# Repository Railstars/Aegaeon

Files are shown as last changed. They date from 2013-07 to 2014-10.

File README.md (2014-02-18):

Aegaeon
=======

A feature-rich, NMRA standards compliant DCC decoder built around the Atmel ATtiny84A.

This project comprises hardware, firmware, and documentation for the Railstars Aegaeon series of [NMRA DCC decoders](http://en.wikipedia.org/wiki/Digital_Command_Control).

The Intent
----------

Let's be honest: Most decoders manufactured in North America kinda suck. We can do better. I want to harness the power of open source development to put together the finest range of decoders available, anywhere. This project has multiple goals:
* NMRA standard conformance
* Robustness: decoders should be fault-tolerant, and compatible with widest range of other DCC equipment
* Size: Modern technology permits really tiny decoders
* Features: There is no excuse not to have the best feature set possible

Hardware
--------

The hardware features an Atmel ATtiny84A microcontroller, a high-current H-Bridge with BEMF feedback, and two high-current open-collector outputs for lighting effects.

### Features

* Ultra-compact size (approx. 11mm x 6.7mm)
* 1A motor outputs
* Feedback motor control (aka BEMF)
* 16KHz or 32KHz motor operating modes
* Two high-current (300mA) function outputs
* Debugging header for use with DEBUGwire devices like Atmel JTAGICE mk2
* Trimming of internal RC oscillator is necessary for operation, requires Atmel AVRISP, a copy of stk500.exe, and MS DOS to calibrate. (Welcome to the 21st century!)

Firmware
--------

The firmware is written in pure C, and can be conditionally compiled for one of three possible configurations (motor only; motor + two functions; H-Bridge-driven function-only). Feature packed, and fully NMRA standards compliant, guaranteed by a stringent set of unit tests (in UnitTests folder, includes Xcode and NetBeans projects so you can run them straight on your Mac or PC).

### Features

* Momentum, 3-step and 28-step speed tables
* Button-controllable shunting mode
* Configurable function directionality, brightness, and Rule 17 dimming effects
* Configurable, button-controllable animations:
    * Strobe
    * Double strobe
    * Rotary beacon
    * Random flicker
    * Left/right ditch lights
    * Mars and Gyra lights
* Optional soft-start lighting effect
* Advanced consisting
* Supports Paged, Direct, Physical, and Operations mode programming
* Configurable DC operation, or stop-on-DC.

License
-------

The contents of the firmware folder is licensed under the GPLv3.
All other content is licensed under a Creative Commons Attribution-ShareAlike 3.0 Unported license

The Future
----------

There are a large number of features I would like to add to this product. I need your help!
- [ ] 2-layer PCB with easy-to-solder components for DIY
- [ ] ATmega328p/AT90CAN128 support for Arduino Uno/Railstars Io:duino
- [ ] Visual Studio project for unit tests
- [ ] Arduino project for easy integration into Arduino projects
- [ ] RailCom support (Railstars has a license to the necessary patents to implement RailCom, need to verify that implementing it as an open source project is kosher)
- [ ] On-the-tracks ops-mode bootloader. Ideally Arduino compatible but that might be a stretch. Would certainly require RailCom to work. But wouldn't that be awesome!?

Discussion
----------

You can get support for the Aegaeon software at the Railstars [Support Forum](http://support.railstars.com/index.php?p=/categories/aegaeon-firmware)

Bitdeli Badge (https://bitdeli.com/free "Bitdeli Badge")

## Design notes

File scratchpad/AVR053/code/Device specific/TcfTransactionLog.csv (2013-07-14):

Service | Message | Max | Min | Average | Count | frequency | TimedOut
Stream | setLogBits | 218.3916 | 218.3916 | 218.3916 | 1 | 0

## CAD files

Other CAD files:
scratchpad/AVR053/code/rc_calib.obj

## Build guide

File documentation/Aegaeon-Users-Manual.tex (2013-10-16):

%! program = pdflatex

\documentclass[12pt,letterpaper,draft]{memoir} % for a short document

\usepackage{longtable}
\usepackage{multirow}
\usepackage{url}
\usepackage{makeidx}
\usepackage{etoolbox}

% See the ``Memoir customise'' template for some common customisations
% Don't forget to read the Memoir manual: memman.pdf

\makepagestyle{manual}
\makeevenhead{manual}{}{}{\rightmark}
\makeoddhead{manual}{\rightmark}{}{}
\makeheadrule{manual}{\textwidth}{0.4pt}
\makeevenfoot{manual}{\thepage}{}{\leftmark}
\makeoddfoot{manual}{\leftmark}{}{\thepage}
\makefootrule{manual}{\textwidth}{0.4pt}{\footruleskip}

\makeoddfoot{plain}{}{}{\thepage}
\makeevenfoot{plain}{\thepage}{}{}
\makefootrule{plain}{\textwidth}{0.4pt}{\footruleskip}

\makeatletter
\aliaspagestyle{title}{empty} % suppress the page number after \maketitle
\let\origps@chapter\ps@chapter
\preto\frontmatter{\let\ps@chapter\ps@empty\pagestyle{empty}}
\preto\mainmatter{%
  \cleardoublepage
  \let\ps@chapter\origps@chapter\pagestyle{headings}}
\makeatother

\title{Aegaeon Family User's Manual\\Revision A}
\author{Railstars Limited}
%\date{} % Delete this line to display the current date

\makeindex

%%% BEGIN DOCUMENT
\begin{document}
\maketitle
\newpage

\chapter*{Acknowledgments}

Many people have made Aegaeon possible, and deserve recognition. First of all, Railstars sends its deepest gratitude to the fine folks at \url{http://jnsforum.com}, where this project was conceived, for all their support and encouragement. Thanks especially to Stuart Baker for his feedback and advice during the design stages. A huge thanks to our testers, Timothy Hatch and Ken Shores, without whose help many bugs would have remained unconvered. Ken's assistance in editing this document was also invaluable. And a thanks to my regular employers, Screenhero, Inc., for their encouragement in completeing this project.

Most of all, however, deepest thanks go to Amy Goodman-Wilson and Acadia Goodman-Wilson, whose love and support throughout this process (as well as their tolerance for flux fumes!) will be forever remembered.
\newpage

\tableofcontents* % the asterisk means that the contents itself isn't put into the ToC

\pagestyle{manual}
%%%%%%%%%%%%%%%%%%%%%%%%%%%%%%%%%%%%%%%%%%%%%%%%%%%%%%%%%%%%%%%%%%%%%%%%%%%%%%%%%%%%
%%%%%%%%%%%%%%%%%%%%%%%%%%%%%%%%%%%%%%%%%%%%%%%%%%%%%%%%%%%%%%%%%%%%%%%%%%%%%%%%%%%%
%%%%%%%%%%%%%%%%%%%%%%%%%%%%%%%%%%%%%%%%%%%%%%%%%%%%%%%%%%%%%%%%%%%%%%%%%%%%%%%%%%%%
\chapter{Introduction}

Thank you for purchasing a Railstars Aegaeon digital decoder! With a little care and feeding, your decoder should offer a lifetime of service. We are certain you will be well-pleased.

The Railstars Aegaeon family of digital decoders are the most advanced ultra-compact decoders on the market today. Despite their diminutive size, the Aegaeon family provides unprecedented fine-grain control over every aspect of their operation and configuration, as well as the same high level of robustness you expect from Railstars.

This manual covers everything you need to know about the Aegaeon:L2, Aegaeon:M, and Aegaeon:C digital decoders. Chapter \ref{installation} covers installation of your decoder. Chapters \ref{generalconfiguration}, \ref{motorconfiguration}, and \ref{specialeffectsconfiguration} cover the wide range of configuration options available on your decoder. Chapter \ref{operations} covers operating your decoder on your layout. Finally, Chapter \ref{troubleshooting} covers the steps you should take when something goes wrong.

\section{What's In a Name?}

The Aegaeon family of digital decoders is named for one of Saturn's moons. This natural satellite is Saturn's smallest moon, and is considered the source of one of Saturn's rings. The moon was, in turn, named for one of the hundred-armed giants of Greek mythology, the hecatonchires, who helped overthrow the Titans. Seems a fitting name to us!

%%%%%%%%%%%%%%%%%%%%%%%%%%%%%%%%%%%%%%%%%%%%%%%%%%%%%%%%%%%%%%%%%%%%%%%%%%%%%%%%%%%%
%%%%%%%%%%%%%%%%%%%%%%%%%%%%%%%%%%%%%%%%%%%%%%%%%%%%%%%%%%%%%%%%%%%%%%%%%%%%%%%%%%%%
%%%%%%%%%%%%%%%%%%%%%%%%%%%%%%%%%%%%%%%%%%%%%%%%%%%%%%%%%%%%%%%%%%%%%%%%%%%%%%%%%%%%
\chapter{Tools \& Installation}
\label{installation}
Each of the various decoders in the Aegaeon family serves a specific purpose, and therefore each is installed in a slightly different manner. The following sections will help you to choose the best decoder for your project, and guide you through the installation proceedure.

%%%%%%%%%%%%%%%%%%%%%%%%%%%%%%%%%%%%%%%%%%%%%%%%%%%%%%%%%%%%%%%%%%%%%%%%%%%%%%%%%%%%
\section{Choosing the Right Decoder}

Each member of the Aegaeon family is designed for a specific purpose. Choose the right decoder for the right task.

\begin{description}
\item[Aegaeon:L2] is designed to drive a single motor and up to two LEDs or bulbs.
\item[Aegaeon:M] is designed to drive a single motor, without any lighting.
\item[Aegaeon:C] is designed for lit cab cars, passenger cars with marker lights, or lit dummy locomotives---anything without a motor. The :C is especially designed for models whose lighting circuits are too small or complicated to cut up (most other DCC decoders require you to partially dismantle the lighting circuits).
\end{description}

Each of these decoders is best suited to a particular kind of model:
\begin{description}
\item[Locomotive with headlights] Aegaeon:L2
\item[Locomotive without headlights] Aegaeon:M
\item[``Helper'' motorized boxcar] Aegaeon:M
\item[Self-propelled passenger unit] Aegaeon:M (if unlit) or Aegaeon:L2 (if lit)
\item[Business car with marker lights] Aegaeon:C
\item[Observation passenger car with marker lights] Aegaeon:C
\item[Unpowered cab unit] Aegaeon:C
\item[Dummy locomotive with lights] Aegaeon:C
\end{description}

%%%%%%%%%%%%%%%%%%%%%%%%%%%%%%%%%%%%%%%%%%%%%%%%%%%%%%%%%%%%%%%%%%%%%%%%%%%%%%%%%%%%
\section{Tools}

If you have never installed a wire-in decoder before, you will find that a good set of tools and a familiarization with the procedure will make the job immeasurably easier. If you have never soldered before, you might find purchasing a beginner's electronics kit (such as those available from Velleman or Sparkfun) excellent practice without risking your expensive models first.

\begin{description}
\item[Soldering iron] with a reasonably fine tip and a good, wet sponge for cleaning the tip. An inexpensive 30W iron from Radio Shack is a fine starting point.
\item[Solder] containing either 60/40 or (preferably) 63/37 tin/lead ratio, with a rosin core. 0.8mm (0.032in) diameter is about right.
\item[Wire strippers] capable of stripping 30AWG wire.
\item[Safety goggles] because hot solder in the eyes stings pretty bad.
\item[Anti-static or grounding strap] to prevent static shocks from destroying your investment.
\item[Needle-nosed pliers] for when your fingers are too big and soft to hold on tight.
\item[Third hand]---not a real one, although that can be helpful too, but the kind that features several alligator clips on a positionable rail. Look to the local fly-fishing outfitter for an inexpensive model.
\item[Heat-proof work surface] such as an old cutting board. Please do not use this cutting board for food after it has been used for electronics work! Lead poisoning is serious stuff.
\item[Kapton tape] or polyamide tape is useful for electrically isolating large surfaces.
\item[Soldering heat sinks] which look like small, flat-surfaced alligator clips, and are useful for when you have to solder to a surface that makes contact with something meltable nearby.
\item[Continuity checker of multimeter] for checking your solder connections and testing for short circuits.
\item[Jeweler's screw-drivers] in both Phillips (cross) and flat heads.
\item[Spudger] for prying at plastic shells and smoothing wires. This is a pencil-like tool made from nylon, usually with a pointed end and a flatted end. Optional, but helpful.
\item[Jeweler's files] in case you need to make small modifications to the metal frame.
\item[Dremel] or similar, with bits for grinding soft metal. Such a tool is for milling out a larger space in any internal metal frame, which is often necessary in many small-scale locomotives.
\end{description}

%%%%%%%%%%%%%%%%%%%%%%%%%%%%%%%%%%%%%%%%%%%%%%%%%%%%%%%%%%%%%%%%%%%%%%%%%%%%%%%%%%%%
\section{Preparing the Model}

If you have never had your model apart before, this is a good time to familiarize yourself with how the model comes apart and fits together. One common mistake is to reach a point where an installation is nearly complete, only to find that the plastic shell no longer fits back on the model!

While the model is apart, assess it for potential locations to site the decoder. Consider not just the open spaces inside the model, but areas in the frame that could be milled away to create space for the decoder too. Be sure to give an eye to where and how the various wires will run, and whether you will need to cut channels for them in any of the parts to ensure good fit.

While the model is apart, check to see if the manufacturer has placed a capacitor across the motor brushes. Most capacitors appear as a flat tan disk. Although such are rare, if you do see one, it should be removed.

Once the decisions have been made, and you are certain how the model goes together, we can begin with the installation itself.

%%%%%%%%%%%%%%%%%%%%%%%%%%%%%%%%%%%%%%%%%%%%%%%%%%%%%%%%%%%%%%%%%%%%%%%%%%%%%%%%%%%%
\section{Installing Aegaeon:L2}

% TODO write this

The Aegaeon:L2 is designed for TODO and is the most difficult decoder to install. Installation consists of the following steps:
\begin{enumerate}
\item Make space for the decoder.
\item Make space for the wires and trim to length.
\item Isolate the motor from the frame.
\item Isolate the lighting board(s).
\item Solder decoder to the frame or brass/copper pickups.
\item Solder decoder to the motor.
\item Solder decoder to the lighting board(s).
\item Route wires.
\item Test.
\item Reassemble model.
\end{enumerate}

% TODO need to say something about checking stall current, use of resistors with LEDs, lots of diagrams, etc. Also use of bulbs and potential for overheating on DCC.

%%%%%%%%%%%%%%%%%%%%%%%%%%%%%%%%%%%%%%%%%%%%%%%%%%%%%%%%%%%%%%%%%%%%%%%%%%%%%%%%%%%%
\section{Installing Aegaeon:M}

The Aegaeon:M is designed to be a reasonably easy decoder to install. Installation consists of the following steps:
\begin{enumerate}
\item Measure stall current.
\item Make space for the decoder.
\item Make space for the wires and trim to length.
\item Isolate the motor from the frame.
\item Solder decoder to the frame or brass/copper pickups.
\item Solder decoder to the motor.
\item Route wires.
\item Test.
\item Reassemble model.
\end{enumerate}

\subsection{Measure Stall Current}
Aegaeon:M is designed to provide as much as 800mA of current continuously, although most N and HO motors draw far less than that under normal operating conditions. The worst-case draw of a motor is its ``stall current'', that is, the current that it draws when full power is applied, but the motor shaft is held firmly still (which, please note, does not constitute ``normal operating conditions''!). Most modern models will have a stall current well below 800mA, but it is easy to check if you have a multimeter or ammeter.

With the ammeter or multimeter wired in series between the power pack and the track, apply full DC voltage while holding the locomotive firmly down on the tracks. The goal is to prevent the wheels from spinning or slipping, thus stalling the motor. Observe the meter's reading. If it is greater than 800mA, consider using a more powerful decoder than the Aegaeon:M.

\subsection{Make Space for the Decoder}
Many larger models will have plenty of open space inside of them where the decoder could be sited. However in N and Z scales, the options are (both literally and figuratively) much narrower. In many cases, you will have to create a pocket for the decoder by milling out a portion of the metal frame. If you have a hard time determining where to site your Aegaeon:M, consider visiting the Railstars Support Site at \url{http://support.railstars.com}. This website offers a range of pictorial instructions for installing Aegaeon decoders, as well as a friendly support forum where you can ask other Aegaeon users for advice.

\subsection{Make Space for the Wires and Trim to Length}
Siting the decoder is only half the battle. The Aegaeon:M has four wires that must also be positioned. It is quite likely that you may have to cut channels in the metal frame or internal plastic supports to make room for the wires---they may look small, but space is tight inside your model!

First, identifying where each of the four wires can be most easily connected to the model. The Red and Black wires collect the DCC signal and power from the tracks, and will need to be wired to the internal current collectors (some times called pick-ups)---the bits of metal that make electrical contact with the rails. The Orange and Gray wires control the motor, and will need to be wired to the motor brushes. See Figure \ref{M-wiring} for an example of how to wire the Aegaeon:M.

%TODO figure \label{M-wiring}

Holding the Aegaeon:M in place with a little double-sided tape, develop a careful plan for routing each lead. Once you have a satisfactory notion of where each will go, trim back any excess length. Otherwise, all that extra wire is going to need space of its own.

\subsection{Isolate the Motor from the Frame}
Normally, the motor's brushes make electrical contact with the two rails (usually indirectly via the frame, or other metal conductors within the model). Installing the Aegaeon:M requires that we break this connection, so that the decoder can control the motor directly. Find the points of electrical contact between the motor brushes and the rest of the model (often inside the metal frame, but sometimes with soldered wires or other mechanisms). Trim back any wires or long leads connecting the motor to the rest of the model, and use Kapton tape as insulation where the electrical contact is achieved via press-fit (a single layer of tape will suffice).

Sometimes it is not obvious how to isolate the motor. If you find yourself stumped, don't forget about the Raisltars Support Site at \url{http://support.railstars.com}, where you can view pictorial installation guides and ask for advice from other Aegaeon users.

Make sure that the motor really is isolated, using a continuity tester where possible. On some models, it may be nearly impossible to test that the motor is isolated. One simple, but not perfectly reliable, method is to reassemble the model, and see if you can make it move with a standard DC throttle. If the motor does not respond to the throttle, there is a good chance is has been successully isolated; if the motor \textit{does} respond, you have not yet achieved the necessary isolation.

\subsection{Solder Red and Black Wires to the Pickups}
Once the motor is isolated, begin connecting the decoder by soldering in the Red and Black wires. You should have, in an earlier step, identified the best place to connect these wires. Now, the time has come to solder these wires to the internal current collectors that make electrical contact with the rails.

\subsection{Solder Orange and Gray Wires to the Motor Brushes}

The Orange and Gray wires control the motor. Now that we are certain that the motor is isolated from the rails, and the decoder is connected to the rails, solder the Orange and Gray wires to the motor leads.

Once connected, this is a good time to make your first real test. You do not need to fully reassemble the model for this step; but you will need to be able to place it on a programming track. Once on the programming track, attempt to read one of the CVs (see \S\ref{WhatIsACV} for details on what a CV is, and how to read them). If you can read the selected CV, the test is passed. If you cannot, then either the decoder is not making good electrical contact with the rails, or with the motor. In this case, use a continuity checker to determine where the break in the circuit might be.

Once you can read CVs, try placing your model on the main line and controlling it with your DCC throttle. The model should respond to speed commands normally. If not, this is a good sign that your connections are perhaps loose, or you have a cold solder joint that needs to be reworked.

\subsection{Route Wires and Affix Decoder}

Once you are certain that the decoder is wired in securely and properly, route the wires into the channels (if you needed to make channels). A spudger comes in handy for telling wires just where they need to go, and pressing them flat into the channels. Use a little double-sided tape to secure the decoder in place, making sure that it is not touching any metal surface; use some Kapton tape if necessary to provide some electrical isolation. You can tape the metal surfaces in the mode near the decoder site, or wrap the decoder in the tape.

\subsection {Test. Test. Test.}

Once everything is in place, repeat all of the tests above. Try reading and writing CVs; give the model a spin on the main line. Everything should run as expected. If not, don't be discouraged! Better to find out that something has gone wrong now, than after the model has been put back together! Again, if something isn't working, a continuity checker is going to be your best tool for isolating problems.

\subsection{Final Reassembly and Test Again}

Even once the model has passed all the tests with flying colors, your work is not yet done. Reassembling the model is not always easy. It might reveal that you didn't leave enough room for the decoder, or the wires. It might also reveal that one of the connections is still a bit loose, and comes apart under pressure from the plastic shell. Both problems are often easy to spot, because the plastic shell will bulge from the pressure of the installed decoder.

%%%%%%%%%%%%%%%%%%%%%%%%%%%%%%%%%%%%%%%%%%%%%%%%%%%%%%%%%%%%%%%%%%%%%%%%%%%%%%%%%%%%
\section{Installing Aegaeon:C}

The Aegaeon:C is designed to control simple DC lighting boards, and hence is probably the easiest decoder to install. Installation consists of the following steps:
\begin{enumerate}
\item Make space for the decoder.
\item Make space for the wires and trim to length.
\item Isolate the lighting board from the frame.
\item Solder decoder to the frame or brass/copper pickups.
\item Solder decoder to the lighting board.
\item Route wires.
\item Test.
\item Reassemble model.
\end{enumerate}

\subsection{Make Space for the Decoder}
Many larger models will have plenty of open space inside of them where the decoder could be sited. However in N and Z scales, the options are (both literally and figuratively) much narrower. In many cases, you will have to create a pocket for the decoder by milling out a portion of the metal frame. If you have a hard time determining where to site your Aegaeon:M, consider visiting the Railstars Support Site at \url{http://support.railstars.com}. This website offers a range of pictorial instructions for installing Aegaeon decoders, as well as a friendly support forum where you can ask other Aegaeon users for advice.

\subsection{Make Space for the Wires and Trim to Length}
Siting the decoder is only half the battle. The Aegaeon:C has four wires that must also be positioned. It is quite likely that you may have to cut channels in the metal frame or internal plastic supports to make room for the wires---they may look small, but space is tight inside your model!

First, identifying where each of the four wires can be most easily connected to the model. The Red and Black wires collect the DCC signal and power from the tracks, and will need to be wired to the internal current collectors (some times called pick-ups)---the bits of metal that make electrical contact with the rails. The White and Yellow wires control the lighting, and will need to be wired to the two leads on the lighting circuit board. See Figure \ref{C-wiring} for an example of how to wire the Aegaeon:C.

%TODO figure \label{C-wiring}

Holding the Aegaeon:M in place with a little double-sided tape, develop a careful plan for routing each lead. Once you have a satisfactory notion of where each will go, trim back any excess length. Otherwise, all that extra wire is going to need space of its own.

\subsection{Isolate the Lighting Board from the Frame}
Normally, the lighting board's leads make electrical contact with the two rails (usually indirectly via the frame, or other metal conductors within the model). Installing the Aegaeon:C requires that we break this connection, so that the decoder can control the lighting board directly. Find the points of electrical contact between the lighting board leads and the rest of the model (often via simple contact with the metal frame, but sometimes with soldered wires or other mechanisms). Trim back any wires or long leads connecting the lighting board to the rest of the model, and use Kapton tape as insulation where the electrical contact is achieved via press-fit (a single layer of tape will suffice).

Sometimes it is not obvious how to isolate the lighting board. If you find yourself stumped, don't forget about the Raisltars Support Site at \url{http://support.railstars.com}, where you can view pictorial installation guides and ask for advice from other Aegaeon users.

Make sure that the lighting board really is isolated, using a continuity tester where possible. On some models, it may be nearly impossible to test that the lighting board is isolated. One simple, but not perfectly reliable, method is to reassemble the model, and see if you can make it light up with a standard DC throttle. If the lighting does not respond to the throttle, there is a good chance is has been successully isolated; if the lighting \textit{does} respond, you have not yet achieved the necessary isolation.

\subsection{Solder Red and Black Wires to the Pickups}
Once the motor is isolated, begin connecting the decoder by soldering in the Red and Black wires. You should have, in an earlier step, identified the best place to connect these wires. Now, the time has come to solder these wires to the internal current collectors that make electrical contact with the rails.

\subsection{Solder White and Yellow Wires to the Lighting Board Leads}

The White and Yellow wires control the lighting board. Now that we are certain that the lighting board is isolated from the rails, and the decoder is connected to the rails, solder the White and Yellow wires to the lighting board leads.

Once connected, this is a good time to make your first real test. You do not need to fully reassemble the model for this step; but you will need to be able to place it on a DCC-controlled main line. Once on the main line, attempt to control the model with your DCC throttle set to DCC address 3. The lighting should come on, and respond to throttle direction changes. If you can so control the lighting, the test is passed. If you cannot, then either the decoder is not making good electrical contact with the rails, or with the lighting board. In this case, use a continuity checker to determine where the break in the circuit might be.

Unfortunately, the usual programming-track test won't always work with the Aegaegon:C, because reading a CV requires a certain amount of current draw from the programmer. Many modern models use highly efficient LED lighting, which does not draw sufficient current to provide the feedback that the DCC programmer is expecting. Thus, we can only test reliably on the main line.

\subsection{Route Wires and Affix Decoder}

Once you are certain that the decoder is wired in securely and properly, route the wires into the channels (if you needed to make channels). A spudger comes in handy for telling wires just where they need to go, and pressing them flat into the channels. Use a little double-sided tape to secure the decoder in place, making sure that it is not touching any metal surface; use some Kapton tape if necessary to provide some electrical isolation. You can tape the metal surfaces in the mode near the decoder site, or wrap the decoder in the tape.

\subsection {Test. Test. Test.}

Once everything is in place, repeat all of the tests above. Try reading and writing CVs; give the model a spin on the main line. Everything should run as expected. If not, don't be discouraged! Better to find out that something has gone wrong now, than after the model has been put back together! Again, if something isn't working, a continuity checker is going to be your best tool for isolating problems.

\subsection{Final Reassembly and Test Again}

Even once the model has passed all the tests with flying colors, your work is not yet done. Reassembling the model is not always easy. It might reveal that you didn't leave enough room for the decoder, or the wires. It might also reveal that one of the connections is still a bit loose, and comes apart under pressure from the plastic shell. Both problems are often easy to spot, because the plastic shell will bulge from the pressure of the installed decoder.

%%%%%%%%%%%%%%%%%%%%%%%%%%%%%%%%%%%%%%%%%%%%%%%%%%%%%%%%%%%%%%%%%%%%%%%%%%%%%%%%%%%%
\section{It Doesn't Work!}

Sometimes an install doesn't go as expected, and problems arise. If you've followed the directions, and your Aegaeon isn't responding as you expect, or at all, please have a careful read of Chapter \ref{troubleshooting}, and especially \S\ref{FAQ}.

%%%%%%%%%%%%%%%%%%%%%%%%%%%%%%%%%%%%%%%%%%%%%%%%%%%%%%%%%%%%%%%%%%%%%%%%%%%%%%%%%%%%
%%%%%%%%%%%%%%%%%%%%%%%%%%%%%%%%%%%%%%%%%%%%%%%%%%%%%%%%%%%%%%%%%%%%%%%%%%%%%%%%%%%%
%%%%%%%%%%%%%%%%%%%%%%%%%%%%%%%%%%%%%%%%%%%%%%%%%%%%%%%%%%%%%%%%%%%%%%%%%%%%%%%%%%%%
\chapter{General Configuration}
\label{generalconfiguration}
Your Aegaeon decoder will work great straight from the box, but you can tailor its behavior to your specific needs, and the needs of your model, by changing the configuration options provided by the decoder. Such configuration is achieved by storing numbers within special registers called Configuration Variables (or CVs for short).

%%%%%%%%%%%%%%%%%%%%%%%%%%%%%%%%%%%%%%%%%%%%%%%%%%%%%%%%%%%%%%%%%%%%%%%%%%%%%%%%%%%%
\section{What is a `CV'?}
\label{WhatIsACV}
\index{configuration variable}
DCC decoders are configured by writing numerical values to variables within the decoder. These variables, called \textbf{Configuration Variables}, or \textbf{CVs} for short, hold a number between 0 and 255, and keep their values permanently or until overwritten with new values. Each CV has a particular meaning, use, and range of valid values. In the next several sections, each CV available on Aegaeon is discussed in great detail.

The specifics of how to read and write values from and to a particular CV depend upon the DCC system you are using: You should consult your system's manual for details. However, it is worth spending a little time learning about the mechanisms defined by the NMRA and employed by the various manufacturers.

\subsection{Service Mode}

Most DCC systems provide a special output---sometimes called the `service track' or `programming track'---for configuring decoders. These special outputs permit configuring decoders in what is known as `service mode'. Service mode is the most reliable way to configure a decoder, because it permits verification of each step, as well as the reading of the values stored in each CV. All DCC decoders, including the Aegaeon family, can be configured in service mode.

\subsection{Operations Mode}

Some DCC systems permit configuration of decoders while in operation on the layout. This is sometimes called `programming on the main' or `operations mode programming'. The Aegaeon family of decoders can be programmed in operations mode.

Operations mode, while certainly very convenient, is not as reliable as service mode configuration. Operations mode does not provide a general method for verification that a configuration operation succeeded, or for reading the value stored in a CV. Moreover, you must know the decoder's address (see \S\ref{PrimaryAddress}) to be able to configure it using operations mode. If you have forgotten the decoder's address, you \textit{must} use service mode to successfully reset or configure it.

%%%%%%%%%%%%%%%%%%%%%%%%%%%%%%%%%%%%%%%%%%%%%%%%%%%%%%%%%%%%%%%%%%%%%%%%%%%%%%%%%%%%
\section{Primary Address}
\label{PrimaryAddress}
All decoders must be assigned a primary address; this address need not be unique. The address is used to send specific commands to each decoder (or set of decoders with the same address). Aegaeon ships with a default address of 3. As with most modern decoders, Aegaeon gives you two options for setting the decoder address: A short address and a long address. The short address is an older mechanism, and is limited to an upper bound of 127. The long address is a newer mechanism, and is limited to an upper bound of 10239. Which address is used is governed by the setting of CV 29 ``Main Configuration'' (see \S\ref{CV29}).

\subsection{Short Address}
\label{CV1}
Most command stations provide an automated method for setting the short address without having to set the CVs directly. In case yours does not, here is the CV table
\index{configuration variable!CV 001@CV 1}\index{address!short}
\begin{center}
\begin{tabular}{|l|c|c|c|}
\hline
\multicolumn{4}{|c|}{\textbf{CV 1 --- Short Address}} \\ \hline \hline
\textit{Feature} & \textit{Options} & \textit{Default} & \textit{User} \\ \hline
Short Address& 1--127 & 3 &\\ \hline
\end{tabular}
\end{center}

The short address can be entered directly into CV 1 without further calculation. The range of valid addresses is 1--127. Addresses outside this range cannot be written. Please note that some manufacturers' systems do not support short addresses outside of a certain range. For example, Digitrax command stations do not permit short addresses larger than 99. If you want to use an address greater than 99, please make sure your system supports it before attempting to write to this CV.

\subsection{Long Address}
\index{configuration variable!CV 017@CV 17}\index{address!long}
\label{CV17}
\begin{center}
\begin{tabular}{|l|c|c|c|}
\hline
\multicolumn{4}{|c|}{\textbf{CV 17 --- Long Address 1}} \\ \hline \hline
\textit{Feature} & \textit{Options} & \textit{Default} & \textit{User} \\ \hline
Long Address High & 192--231 & 0 &\\ \hline
\end{tabular}
\end{center}

\index{configuration variable!CV 018@CV 18}
\label{CV18}
\begin{center}
\begin{tabular}{|l|c|c|c|}
\hline
\multicolumn{4}{|c|}{\textbf{CV 18 --- Long Address 2}} \\ \hline \hline
\textit{Feature} & \textit{Options} & \textit{Default} & \textit{User} \\ \hline
Long Address Low & 0--255 & 0 &\\ \hline
\end{tabular}
\end{center}

The range of valid long addresses is 1--10239. Please note that some manufacturers' systems do not permit long addresses outside of a certain range; for example, some systems exclude the use of long addresses 1--127. Digitrax systems do not permit addresses greater than 9999.

The long address is larger than can be contained in a single CV, and so must be split up. Given a desired long address, it is somewhat tricky to calculate the values for \textbf{CV 17} and \textbf{CV 18}, and we strongly recommend you use an on-line calculator for this purpose, such as the one available at \url{http://railstars.com/long-address-calculator}.

Notice that you \textit{must} enter the value for CV 17 first, and the value for CV 18 second.

%%%%%%%%%%%%%%%%%%%%%%%%%%%%%%%%%%%%%%%%%%%%%%%%%%%%%%%%%%%%%%%%%%%%%%%%%%%%%%%%%%%%
\section{Decoder Identification}

\subsection{Manufacturer Identification}
\label{ManufacturerIdentification}\index{manufacturer identification}
There are three read-only CVs that provide information on the manufacturer and the firmware used in the decoder. These CVs cannot be written (although see \S\ref{DecoderReset} before you try!).

\index{configuration variable!CV 008@CV 8}
\label{CV8}
\begin{center}
\begin{tabular}{|l|c|c|}
\hline
\multicolumn{3}{|c|}{\textbf{CV 8 --- Manufacturer ID}} \\ \hline \hline
\textit{Feature}& \textit{Default} & \textit{User} \\ \hline
Railstars Limited & 91 & n/a\\ \hline
\end{tabular}
\end{center}

\index{configuration variable!CV 007@CV 7}\index{decoder family identification}
\label{CV7}
\begin{center}
\begin{tabular}{|l|c|c|}
\hline
\multicolumn{3}{|c|}{\textbf{CV 7 --- Decoder Family Identification}} \\ \hline \hline
\textit{Feature}& \textit{Default} & \textit{User} \\ \hline
Aegaeon:L2 & 5 & n/a\\ \hline
Aegaeon:M & 1 & n/a\\ \hline
Aegaeon:C & 4 & n/a\\ \hline
\end{tabular}
\end{center}

The firmware revision is subject to change as the firmware is updated by the manufacturer.
\index{configuration variable!CV 058@CV 58}\index{firmware revision}
\label{CV58}
\begin{center}
\begin{tabular}{|l|c|c|}
\hline
\multicolumn{3}{|c|}{\textbf{CV 58 --- Firmware Revision}} \\ \hline \hline
\textit{Feature}& \textit{Default} & \textit{User} \\ \hline
Revision Number & 1 & n/a\\ \hline
\end{tabular}
\end{center}

\subsection{User Identification}
\label{UserIdentification}\index{user identification}
Two CVs are provided for you to store arbitrary values; typically, these values are used to provide a way to uniquely identify the decoder in some way, or perhaps to record some piece of information of occasional use.

\index{configuration variable!CV 105@CV 105}
\label{CV105}
\begin{center}
\begin{tabular}{|l|c|c|c|}
\hline
\multicolumn{4}{|c|}{\textbf{CV 105 --- User Identification 1}} \\ \hline \hline
\textit{Feature} & \textit{Options} & \textit{Default} & \textit{User} \\ \hline
Freeform data & 0--255 & 0 &\\ \hline
\end{tabular}
\end{center}

\index{configuration variable!CV 106@CV 106}
\label{CV106}
\begin{center}
\begin{tabular}{|l|c|c|c|}
\hline
\multicolumn{4}{|c|}{\textbf{CV 106 --- User Identification 2}} \\ \hline \hline
\textit{Feature} & \textit{Options} & \textit{Default} & \textit{User} \\ \hline
Freeform data & 0--255 & 0 &\\ \hline
\end{tabular}
\end{center}

%%%%%%%%%%%%%%%%%%%%%%%%%%%%%%%%%%%%%%%%%%%%%%%%%%%%%%%%%%%%%%%%%%%%%%%%%%%%%%%%%%%%
\section{When Things Go Wrong: Decoder Reset}
\label{DecoderReset}\index{reset}
If you make a mistake, or the decoder becomes difficult, you can perform a decoder reset. There are two kinds of reset: A full reset that restores the decoder to the factory settings, and a partial reset that preserves the Advanced Speed Curve (aka 28-Step Speed Table; see \S\ref{AdvancedSpeedCurve}), as this is tedious to have to re-enter. Notice that you may have to put the decoder on the service track to successfully reset it, although it can be done on the main if the decoder is responding to the proper address (and you know what that address is).

To make the reset, you write a specific value into CV 8, the (read-only) CV that contains the manufacturer's ID. The value written here is not stored, but used as a trigger to perform the reset operation.

\index{configuration variable!CV 008@CV 8}
\begin{center}
\begin{tabular}{|l|cc|}
\hline
\multicolumn{3}{|c|}{\textbf{CV 8 --- Reset}} \\ \hline \hline
\textit{Feature}& \multicolumn{2}{c|}{\textit{Options}}  \\ \hline
\multirow{2}{*}{Type of Reset}  & Factory Reset & 8\\ 
& Partial Reset & 9 \\ \hline
\end{tabular}
\end{center}

%%%%%%%%%%%%%%%%%%%%%%%%%%%%%%%%%%%%%%%%%%%%%%%%%%%%%%%%%%%%%%%%%%%%%%%%%%%%%%%%%%%%
\section{Basic Configuration: CV 29}

CV 29 controls the most basic functionality of the decoder. This CV is standardized by the NMRA, and actually controls a variety of unrelated attributes, each of which is discussed in detail below.

\index{configuration variable!CV 029@CV 29}
\label{CV29}
\begin{center}
\begin{tabular}{|l|lc|c|c|}
\hline
\multicolumn{5}{|c|}{\textbf{CV 29 --- Basic Configuration}} \\ \hline \hline
\textit{Feature} & \multicolumn{2}{c|}{\textit{Options}} & \textit{Default} & \textit{User} \\ \hline
\multirow{2}{*}{Direction of Travel} & \textbf{Forward}	 & \textbf{0} & \multirow{2}{*}{0} &\\
& Reversed & 1 & & \\ \hline
Speed Control & \textbf{28/128-Step} & \textbf{2} & 2 & 2\\ \hline
\multirow{2}{*}{Run on DC} & Disabled & 0 & \multirow{2}{*}{4} & \\
& \textbf{Enabled} & \textbf{4} & & \\ \hline
\multirow{2}{*}{Speed Curve} & \textbf{Basic} & \textbf{0}  & \multirow{2}{*}{0}& \\
& Advanced & 16 & &\\ \hline
\multirow{2}{*}{Addressing} & \textbf{Short} & \textbf{0} & \multirow{2}{*}{0} & \\
& Long & 32 & &\\ \hline \hline
\multicolumn{3}{|r|}{\textit{Total}} & 6 &\\ \hline
\end{tabular}
\end{center}

\subsection{Direction of Travel}
\label{DC29directionoftravel}\index{direction of travel}
All DCC-equipped locomotives have a well-defined forward and reverse facing. The forward direction is determined by which motor terminal the orange lead is wired to---it should be wired to the right-hand, or engineer's side of the motor. However, there will be times when you need to define the forward direction, perhaps because you wired the motor incorrectly, or because the locomotive will normally be run in reverse, or some other reason. The Direction of Travel feature of CV 29 allows you to define which way is forward. If the locomotive runs in the opposite of the expected direction, change the option for this feature..

\subsection{Speed Control}
\label{CV29speedcontrol}\index{speed control}
This feature is meant for compatibility with older command stations. Aegaeon does not permit modification of this feature, and it is only listed for completeness. Aegaeon decoders will, nevertheless, operate correctly on older command stations, so there is nothing to worry about! %If your command station is of relatively recent vintage, leave this options set to \textit{28/128-step}. In short, there are three different ways that a command station can direct a decoder's speed---with a 14-step, a 28-step, or a 128-step instruction. Most contemporary command stations will issue 28- or 128-step instructions, where older command stations use the older 14-step instruction. Aegaeon will respond properly to 14-step instructions regardless of this option setting. However, the 14-step instruction also contains the state of lighting function \textbf{FL}. If, when using an older command station, the lights attached to your Aegaeon do not respond, consider selecting the \textit{13-Step} option for this feature.

\subsection{Run on DC}
\label{CV29runondc}\index{DC operations}
When enabled, this feature permits the use of your Aegeaon-equipped locomotive on analog layouts. Aegaeon is designed for the smoothest possible low-speed response to analog throttles. As an alternative, you may disable this feature, in which case Aegaeon will bring the motor to a halt when it encounters an analog signal. This option permits you to automate stopping at signals and stations by switching the track between a DCC and a DC signal.

\subsection{Speed Curve}
\label{CV29SpeedCurve}
Speed curves define the relationship between Speed Steps and motor voltage. By default, the highest speed step is mapped to 100\% voltage, and the lowest speed step to about 0.4\% voltage. You may define the mapping between speed steps and voltage in one of two ways: With a \textit{Basic Speed Curve}, or an \textit{Advanced Speed Curve}.

%TODO fix this
\index{speed curve!basic}The Basic Speed Curve is the simplest to set up, and suffices for most applications. Here, you have three entries that tell the decoder how much voltage to apply to the motor at the first speed step, at the middle speed step (step TODO for 28-step instructions, and TODO of 128-step instructions), and at the largest speed step. Setting up the Basic Speed Curve is explained in \S\ref{BasicSpeedCurve} (pg. \pageref{BasicSpeedCurve}).

\index{speed table!advanced}The Advanced Speed Curve is more involved to set up, but provides a great deal more flexibility in defining the relationship between speed steps and voltages, as it offers 28 points of control. The Advanced Speed Curve permits non-linear response curves, allowing, for example, finer control at low speeds. Setting up the Advanced Speed Curve is explained in \S\ref{AdvancedSpeedCurve} (pg. \pageref{AdvancedSpeedCurve}).

\subsection{Addressing}
\index{address}
All decoders must be assigned an address. The address can take one of two distinct forms: Long Address or Short Address. The only difference between the two forms is the largest address that can be assigned. Aegaeon will automatically set this bit when you assign a short or long address to the decoder, so in general you need not worry about it. However, you can manually set which form of addressing you would like by setting this option yourself.

Notice that if one of the assigned short or long address is `0', the non-zero address is used regardless of this feature's setting. If both addresses are assigned to `0', the Aegaeon defaults to having the short address 3. This is a fail-safe to prevent the decoder from becoming unreachable on the main line in case a mistake is made when setting the decoder's address.

The observant will notice that there is an overlap in the range of these two addresses such that a long address of, e.g., 3 is \textit{distinct} from a short address of 3. This is an unfortunate side-effect of having two distinct address spaces. Most command stations will not permit you to assign a long address with a value within the valid range of short addresses---that is, will not permit you to assign a long address of, e.g., 3, forcing such addresses to be short.

%%%%%%%%%%%%%%%%%%%%%%%%%%%%%%%%%%%%%%%%%%%%%%%%%%%%%%%%%%%%%%%%%%%%%%%%%%%%%%%%%%%%
\section{Consisting}
\label{consisting}
Often it is desirable to run multiple locomotives or other rolling stock containing decoders as a single unit, called a consist. The Aegaeon family supports two mechanisms: permanent consisting, and advanced consisting.

\subsection{Permanent Consisting}
\index{consisting!permanent}
Permanent consisting is the simplest way to define a consist. It is achieved simply by assigning the same address to each element of the consist. This method of consisting is recommended for multiple units such as commuter trains or high-speed rail where the configuration is fixed and several decoders might be used. Permanent consisting insures that the entire train behaves as a solitary unit, each decoder acting in lock-step with the others. It also eases configuration, as often you will have multiple decoders that must be configured identically---with permanent consisting, you need only issue configuration commands once, as all of the decoders are programmed in parallel.

\subsection{Advanced Consisting}
\label{AdvancedConsisting}\index{consisting!advanced}
Advanced consisting is slightly more complex, but also more flexible. This is the recommended method for temporarily consisting several locomotives, as this method allows you to define the behavior of the locomotive in a consist separately from the behavior when running solo. 

Advanced consisting is activated by writing a non-zero value into CV 19, Consist Address. This is a secondary address; you can issue commands to the decoder using either the primary address (see \S\ref{PrimaryAddress}) or the consist address. Commands issued to the consist address are acted upon by \textit{all} decoders with that consist address. Assigning a value to CV 19 also activates the consist-specific lighting and motor behaviors, if configured (see \S\ref{LightingInConsist} and \S\ref{MotorControlInConsist}). The valid range of consist addresses is 1--127. In addition, the consist address also determines the direction of travel for the locomotive in the consist, as sometimes you will want to place a locomotive reversed within the consist.

\index{configuration variable!CV 019@CV 19}
\label{CV19}
\begin{center}
\begin{tabular}{|l|lc|c|c|}
\hline
\multicolumn{5}{|c|}{\textbf{CV 19 --- Consist Address}} \\ \hline \hline
\textit{Feature} & \multicolumn{2}{c|}{\textit{Options}} & \textit{Default} & \textit{User} \\ \hline
\multirow{2}{*}{Address} & \textbf{Inactive} & \textbf{0} & \multirow{2}{*}{0} & \\
									  & Active & 1--127 & & \\ \hline
\multirow{2}{*}{Direction of Travel} & \textbf{Forward}	 & \textbf{0} & \multirow{2}{*}{0} &\\
																		& Reversed & 128 & & \\ \hline \hline
\multicolumn{3}{|r|}{\textit{Total}} & 0 &\\ \hline
\end{tabular}
\end{center}

%%%%%%%%%%%%%%%%%%%%%%%%%%%%%%%%%%%%%%%%%%%%%%%%%%%%%%%%%%%%%%%%%%%%%%%%%%%%%%%%%%%%
\section{Odds and Ends}
\subsection{Timeout}
\index{timeout}
A decoder which is not being actively used, yet remains running on the layout can be a liability. The timeout, defined by CV 11, is the amount of time that a decoder that has not received any commands will continue running at its current speed. Once the timeout limit is reached, the decoder will bring the motor to an emergency stop. A value of ``0'' disables this feature so that the decoder will continue running indefinitely in the abscence of explicit commands.

\index{configuration variable!CV 011@CV 11}
\label{CV11}
\begin{center}
\begin{tabular}{|l|lc|c|c|}
\hline
\multicolumn{5}{|c|}{\textbf{CV 11 --- Timeout}} \\ \hline \hline
\textit{Feature} & \multicolumn{2}{c|}{\textit{Options}} & \textit{Default} & \textit{User} \\ \hline
Timeout,& \textbf{Disabled}	 & \textbf{0} & \multirow{2}{*}{0} &\\
in seconds & Active & 1--255 & & \\ \hline
\end{tabular}
\end{center}

\subsection{Decoder Lock}
Some models will have multiple decoders in them. Decoder lock is a feature that is designed to help you configure each of the decoders in that one model individually without having to remove them one at a time. CV 16 is the \textit{lock}, and contains a value that is unique to each decoder inside the model (they do not have to be globally unique, just among the decoders inside the model)---this CV \textit{must} be set prior to installing the decoder. Once the decoder is installed, \textit{do not reconfigure CV 16!}---if you do, you will have to extract the decoder and reprogram it on its own. CV 15 is the \textit{key}: Aegaeon (and other decoders that implement this feature) will only accept CV programming commands when the value in the key (CV 15) matches the value in the lock (CV 16). Thus, to configure a locked decoder, program first the key to match the lock of the decoder you wish to access.

Notice that this feature is disabled when the key, CV 16, is programmed to 0, the factory default.

\index{configuration variable!CV 016@CV 16}\index{decoder lock}
\label{CV16}
\begin{center}
\begin{tabular}{|l|c|c|c|c|}
\hline
\multicolumn{5}{|c|}{\textbf{CV 16 --- Decoder Lock}} \\ \hline \hline
\textit{Feature} & \multicolumn{2}{c|}{\textit{Options}} & \textit{Default} & \textit{User} \\ \hline
\multirow{2}{*}{Lock Address} & \textbf{Disabled} & \textbf{0} & \multirow{2}{*}{0} & \\
 & Enabled & 1--255 &  &\\ \hline
\end{tabular}
\end{center}

\index{configuration variable!CV 015@CV 15}
\label{CV15}
\begin{center}
\begin{tabular}{|l|c|c|c|}
\hline
\multicolumn{4}{|c|}{\textbf{CV 15 --- Decoder Key}} \\ \hline \hline
\textit{Feature} & \textit{Options} & \textit{Default} & \textit{User} \\ \hline
Key Value & 1--255 & 0 &\\ \hline
\end{tabular}
\end{center}

\subsection{Operations Mode Acknowledgment}
Because programming CVs in Operations Mode offers no feedback to your programmer when CV programming is successful, Aegaeon can optionally provide visual feedback to you. Aegaeon:M and :L2 decoders give a short pulse to the motor, while Aegaeon:C flashes the headlights to indicate that programming a CV was successful. This feature is on by default---CV 47 controls the behavior of this feature.

Please note that this feature is \textit{not} to be confused with Lenz RailCom\textsuperscript{\textregistered}  feedback or Digitrax Transponding feedback. This basic acknowledgement is meant only to provide a visual cue to the user.

\index{configuration variable!CV 047@CV 47}\index{operations mode acknowledgment}
\label{CV47}
\begin{center}
\begin{tabular}{|l|lc|c|c|}
\hline
\multicolumn{5}{|c|}{\textbf{CV 47 --- Operations Mode Acknowledgment}} \\ \hline \hline
\textit{Feature} & \multicolumn{2}{c|}{\textit{Options}} & \textit{Default} & \textit{User} \\ \hline
\multirow{2}{*}{Acknowledgement} & \textbf{On}	 & \textbf{1} & \multirow{2}{*}{1} &\\
													& Off & 0 & & \\ \hline
\end{tabular}
\end{center}

%%%%%%%%%%%%%%%%%%%%%%%%%%%%%%%%%%%%%%%%%%%%%%%%%%%%%%%%%%%%%%%%%%%%%%%%%%%%%%%%%%%%
%%%%%%%%%%%%%%%%%%%%%%%%%%%%%%%%%%%%%%%%%%%%%%%%%%%%%%%%%%%%%%%%%%%%%%%%%%%%%%%%%%%%
%%%%%%%%%%%%%%%%%%%%%%%%%%%%%%%%%%%%%%%%%%%%%%%%%%%%%%%%%%%%%%%%%%%%%%%%%%%%%%%%%%%%
\chapter{Motor Configuration}
\label{motorconfiguration}
This chapter applies only to the Aegaeon:L2 and :M decoders.

The Aegaeon:L2 and :M decoders provide a number of options for configuring the motor behavior, allowing you to tailor the decoder to the model and enhancing the operation of your model, including:

\begin{itemize}
\item Basic (3-Step) and Advanced (28-Step) Speed Curves
\item Independent forward and reverse trim
\item Independent acceleration and deceleration (momentum)
\item Feedback control of the motor (BEMF)
\begin{itemize}
\item With separate settings for solo and consisted operation
\end{itemize}
\item Triggerable shunting mode (half speed)
\item Selectable motor control frequency
\item Configurable kick-start pulse to overcome stiction
\end{itemize}

%%%%%%%%%%%%%%%%%%%%%%%%%%%%%%%%%%%%%%%%%%%%%%%%%%%%%%%%%%%%%%%%%%%%%%%%%%%%%%%%%%%%
\section{Tailoring to the Motor}
\label{TailoringToMotor}

\subsection{Motor Control Frequency}
\label{MotorControlFrequency}\index{motor!frequency}
Aegaeon, like all decoders, uses pulsed voltages for precise motor control. The frequency of these pulses can be selected within Aegaeon with a CV setting. 32KHz mode, the default, provides the quietest operation, at the cost, in some motors, of somewhat decreased torque (pulling ability). 16KHz mode increases the available torque slightly, but at the cost of a little bit of high-pitched hum from the motor. Most motors will respond to either mode more or less equally well; only adjust this setting if you are experiencing a significant loss of pulling power with Aegaeon installed.

\index{configuration variable!CV 059@CV 59}
\label{CV59}
\begin{center}
\begin{tabular}{|l|lc|c|c|}
\hline
\multicolumn{5}{|c|}{\textbf{CV 59 --- Motor Control Frequency}} \\ \hline \hline
\textit{Feature} & \multicolumn{2}{c|}{\textit{Options}} & \textit{Default} & \textit{User} \\ \hline
\multirow{2}{*}{Frequency}	& \textbf{32KHz}	& \textbf{1} 	& \multirow{2}{*}{1} 	&\\
			& 16KHz 		& 0 			& 				& \\ \hline
\end{tabular}
\end{center}

\subsection{Kick Start}
\label{KickStart}\index{motor!static friction}\index{kick start!see {motor, static friction}}
Many DC motors, especially in older models, tend to stick a bit when accelerating from a dead stop. This phenomenon is often called `static friction', or `stiction' for short. You can observe it at work by applying throttle until the locomotive first begins to move, then backing the throttle off---if the locomotive slows down, and keeps running, then you've got static friction, and should consider applying a kick start.

Kick-starting the motor is a method of overcoming static friction by applying a brief pulse of full voltage, to jolt the motor into action, and then immediately backing the throttle to the desired speed. Aegaeon allows you to configure the length of the pulse. When adjusting this feature, we recommend starting from a value of one, and gradually working upwards, rather than jumping directly to a larger value. Reasonable values will probably lie between 1 and 10.

\index{configuration variable!CV 065@CV 65}
\label{CV65}
\begin{center}
\begin{tabular}{|l|c|c|c|}
\hline
\multicolumn{4}{|c|}{\textbf{CV 65 --- Kick Start}} \\ \hline \hline
\textit{Feature} & \textit{Options} & \textit{Default} & \textit{User} \\ \hline
Pulse length in ms & 0--255 & 0 &\\ \hline
\end{tabular}
\end{center}

\subsection{Motor Trim}
\label{MotorTrim}\index{motor!trim}
Often, a DC motor does not spin at the same rate when moving forward as when moving in reverse. Sometimes this difference can be quite large, in fact. Forward and Reverse Trim settings make it easy to tune the motor so that it will spin at the same rate in both directions. Typically, you will only need to set one or the other of these settings, but both are provided for your convenience.

The final amount of trim is determined by dividing the value of the trim setting by 128. Thus, for example, a value of 64 results in a 50\% reduction in speed; a value of 192 results in a 150\% increase in speed.

\index{configuration variable!CV 066@CV 66}
\label{CV66}
\begin{center}
\begin{tabular}{|l|lc|c|c|}
\hline
\multicolumn{5}{|c|}{\textbf{CV 66 --- Forward Trim}} \\ \hline \hline
\textit{Feature} & \multicolumn{2}{c|}{\textit{Options}} & \textit{Default} & \textit{User} \\ \hline
\multirow{4}{*}{Trim Amount}	& Disabled		& \textbf{0} 	& \multirow{4}{*}{0} 	&\\
			& Decrease speed 	& 1--127 		& 				& \\
			& No trim (disabled) 	& 128 		& 				& \\
			& Increase speed 	& 129--255 	& 				& \\ \hline
\end{tabular}
\end{center}

\index{configuration variable!CV 095@CV 95}
\label{CV95}
\begin{center}
\begin{tabular}{|l|lc|c|c|}
\hline
\multicolumn{5}{|c|}{\textbf{CV 95 --- Reverse Trim}} \\ \hline \hline
\textit{Feature} & \multicolumn{2}{c|}{\textit{Options}} & \textit{Default} & \textit{User} \\ \hline
\multirow{4}{*}{Trim Amount}	& Disabled		& \textbf{0} 	& \multirow{4}{*}{0} 	&\\
			& Decrease speed 	& 1--127 		& 				& \\
			& No trim (disabled) 	& 128 		& 				& \\
			& Increase speed 	& 129--255 	& 				& \\ \hline
\end{tabular}
\end{center}

%%%%%%%%%%%%%%%%%%%%%%%%%%%%%%%%%%%%%%%%%%%%%%%%%%%%%%%%%%%%%%%%%%%%%%%%%%%%%%%%%%%%
\section{Momentum}
\label{Momentum}\index{momentum}\index{inertia!see {momentum}}\index{acceleration!see {momentum}}\index{deceleration!see {momentum}}
One of the great features of DCC is that it allows you to simulate the momentum of hauling a heavy train. Even if you would rather not perform a simulation, a small amount of momentum will help increase the life of your DC motor by shielding it from sudden changes in voltage, without affecting its responsiveness. Every motor is different, and every train is different, so some experimentation will be necessary to determine what feels right to you. 

Momentum is simulated by applying a fixed acceleration or deceleration rate to the motor. The acceleration and deceleration rates are calculated by taking the value in the setting, and multiplying by 0.896 $\mathit{speed steps}/s^2$. A value of 0 turns this feature off.

\index{configuration variable!CV 003@CV 3}
\label{CV3}
\begin{center}
\begin{tabular}{|l|c|c|c|}
\hline
\multicolumn{4}{|c|}{\textbf{CV 3 --- Acceleration Rate}} \\ \hline \hline
\textit{Feature} & \textit{Options} & \textit{Default} & \textit{User} \\ \hline
Acceleration rate & 0--255 & 0 &\\ \hline
\end{tabular}
\end{center}

\index{configuration variable!CV 004@CV 4}
\label{CV4}
\begin{center}
\begin{tabular}{|l|c|c|c|}
\hline
\multicolumn{4}{|c|}{\textbf{CV 4 --- Deceleration Rate}} \\ \hline \hline
\textit{Feature} & \textit{Options} & \textit{Default} & \textit{User} \\ \hline
Deceleration rate & 0--255 & 0 &\\ \hline
\end{tabular}
\end{center}

%%%%%%%%%%%%%%%%%%%%%%%%%%%%%%%%%%%%%%%%%%%%%%%%%%%%%%%%%%%%%%%%%%%%%%%%%%%%%%%%%%%%
\section{Basic Speed Curve}
\label{BasicSpeedCurve}\index{speed curve!basic}\index{speed table!see {speed curve}}

Speed curves, sometimes called speed tables, allow you to tailor the motor's response to a given throttle position. Normally, the response is linear---the motor's speed increases proportional to the throttle setting. Sometimes, however, you would like to change this response curve. For example, if your motor does \textit{not} linearly respond to the throttle, you can use these values to attain a linear response. Or perhaps you want finer control over low speed operations, at the expense of coarser control over high speed operations.

The Basic Speed Curve gives you three settings to tune; if you require finer control, consider activating the Advanced Speed Curve discussed in \S\ref{AdvancedSpeedCurve}. To activate the Basic Speed Curve, please see Basic Configuration in CV29 in \S\ref{CV29SpeedCurve}.

The start voltage is the voltage applied to the motor at the first speed step beyond stop. The mid-range voltage is the voltage applied to the motor at the middle speed step. The maximum voltage is the voltage applied to the motor at full throttle. In general, a value of 0 means zero voltage, and 255 means full voltage.

\index{configuration variable!CV 002@CV 2}
\label{CV2}
\begin{center}
\begin{tabular}{|l|c|c|c|}
\hline
\multicolumn{4}{|c|}{\textbf{CV 2 --- Start Voltage}} \\ \hline \hline
\textit{Feature} & \textit{Options} & \textit{Default} & \textit{User} \\ \hline
Voltage & 0--255 & 1 &\\ \hline
\end{tabular}
\end{center}

\index{configuration variable!CV 006@CV 6}
\label{CV6}
\begin{center}
\begin{tabular}{|l|lc|c|c|}
\hline
\multicolumn{5}{|c|}{\textbf{CV 6 --- Mid-Range Voltage}} \\ \hline \hline
\textit{Feature} & \multicolumn{2}{c|}{\textit{Options}} & \textit{Default} & \textit{User} \\ \hline
\multirow{2}{*}{Voltage}		& Half-voltage		& \textbf{0} or 1 & \multirow{2}{*}{0} 	&\\
			& User setting	 	& 2--255 		& 				& \\ \hline
\end{tabular}
\end{center}

\index{configuration variable!CV 005@CV 5}
\label{CV5}
\begin{center}
\begin{tabular}{|l|lc|c|c|}
\hline
\multicolumn{5}{|c|}{\textbf{CV 5 --- Maximum Voltage}} \\ \hline \hline
\textit{Feature} & \multicolumn{2}{c|}{\textit{Options}} & \textit{Default} & \textit{User} \\ \hline
\multirow{2}{*}{Voltage}		& Full-voltage		& \textbf{0} or 1 & \multirow{2}{*}{0} 	&\\
			& User setting	 	& 2--255 		& 				& \\ \hline
\end{tabular}
\end{center}

%TODO insert some charts with examples

%%%%%%%%%%%%%%%%%%%%%%%%%%%%%%%%%%%%%%%%%%%%%%%%%%%%%%%%%%%%%%%%%%%%%%%%%%%%%%%%%%%%
\section{Advanced Speed Curve}
\label{AdvancedSpeedCurve}\index{speed curve!advanced}

Speed curves, sometimes called speed tables, allow you to tailor the motor's response to a given throttle position. Normally, the response is linear---the motor's speed increases proportional to the throttle setting. Sometimes, however, you would like to change this response curve. For example, if your motor does \textit{not} linearly respond to the throttle, you can use these values to attain a linear response. Or perhaps you want finer control over low speed operations, at the expense of coarser control over high speed operations.

The Advanced Speed Curve gives you twenty-eight settings to tune; if you do not require such fine control, consider activating the Basic Speed Curve discussed in \S\ref{BasicSpeedCurve}. To activate the Advanced Speed Curve, please see Basic Configuration in CV29 in \S\ref{CV29SpeedCurve}.

The first setting in the Advanced Speed Curve is the voltage applied to the motor at the first speed step beyond stop. Each CV after the first defines the motor voltage at the next speed step in 28-step mode. In 128-step mode, the values between CVs are interpolated. Thus, CV 68 is for step 6 (of 128), CV 69 for step 11, with the appropriate values for steps 7--10 automatically calculated.

Because setting up the Advanced Speed Curve is so tedious, you might consider using DecoderPro\textsuperscript{\textregistered}, freely available as part of the JMRI\textsuperscript{\textregistered} software suite (available at \url{jmri.sourceforge.net/download/}), to automate this process. Moreover, if you wish to preserve your hard work through a decoder reset, use the partial reset method described in \S\ref{DecoderReset}.

\index{configuration variable!CV 067@CV 67}\index{configuration variable!CV 068@CV 68}
\index{configuration variable!CV 068@CV 69}\index{configuration variable!CV 070@CV 70}
\index{configuration variable!CV 071@CV 71}\index{configuration variable!CV 072@CV 72}
\index{configuration variable!CV 073@CV 73}\index{configuration variable!CV 074@CV 74}
\index{configuration variable!CV 075@CV 75}\index{configuration variable!CV 076@CV 76}
\index{configuration variable!CV 077@CV 77}\index{configuration variable!CV 078@CV 78}
\index{configuration variable!CV 079@CV 79}\index{configuration variable!CV 080@CV 80}
\index{configuration variable!CV 081@CV 81}\index{configuration variable!CV 082@CV 82}
\index{configuration variable!CV 083@CV 83}\index{configuration variable!CV 084@CV 84}
\index{configuration variable!CV 085@CV 85}\index{configuration variable!CV 086@CV 86}
\index{configuration variable!CV 087@CV 87}\index{configuration variable!CV 088@CV 88}
\index{configuration variable!CV 089@CV 89}\index{configuration variable!CV 090@CV 90}
\index{configuration variable!CV 091@CV 91}\index{configuration variable!CV 092@CV 92}
\index{configuration variable!CV 093@CV 93}\index{configuration variable!CV 094@CV 94}
\label{CV67}\label{CV68}
\label{CV69}\label{CV70}
\label{CV71}\label{CV72}
\label{CV73}\label{CV74}
\label{CV75}\label{CV76}
\label{CV77}\label{CV78}
\label{CV79}\label{CV80}
\label{CV81}\label{CV82}
\label{CV83}\label{CV84}
\label{CV85}\label{CV86}
\label{CV87}\label{CV88}
\label{CV89}\label{CV90}
\label{CV91}\label{CV92}
\label{CV93}\label{CV94}
\begin{center}
\begin{longtable}{|l|c|c|c|c|}
\hline
\multicolumn{5}{|c|}{\textbf{CV 67--94 --- Advanced Speed Table}} \\ \hline \hline
\textit{CV}	& \textit{Step}	& \textit{Voltage}	& \textit{Default}	& \textit{User}	\\ \hline
67		& 1			& 0--255			& 1				&			\\ \hline
68		& 2			& 0--255			& 10				&			\\ \hline
69		& 3			& 0--255			& 19				&			\\ \hline
70		& 4			& 0--255			& 29				&			\\ \hline
71		& 5			& 0--255			& 38				&			\\ \hline
72		& 6			& 0--255			& 48				&			\\ \hline
73		& 7			& 0--255			& 57				&			\\ \hline
74		& 8			& 0--255			& 66				&			\\ \hline
75		& 9			& 0--255			& 76				&			\\ \hline
76		& 10			& 0--255			& 85				&			\\ \hline
77		& 11			& 0--255			& 95				&			\\ \hline
78		& 12			& 0--255			& 104			&			\\ \hline
79		& 13			& 0--255			& 113			&			\\ \hline
80		& 14			& 0--255			& 123			&			\\ \hline
81		& 15			& 0--255			& 132			&			\\ \hline
82		& 16			& 0--255			& 142			&			\\ \hline
83		& 17			& 0--255			& 151			&			\\ \hline
84		& 18			& 0--255			& 160			&			\\ \hline
85		& 19			& 0--255			& 170			&			\\ \hline
86		& 20			& 0--255			& 179			&			\\ \hline
87		& 21			& 0--255			& 189			&			\\ \hline
88		& 22			& 0--255			& 198			&			\\ \hline
89		& 23			& 0--255			& 207			&			\\ \hline
90		& 24			& 0--255			& 217			&			\\ \hline
91		& 25			& 0--255			& 226			&			\\ \hline
92		& 26			& 0--255			& 236			&			\\ \hline
93		& 27			& 0--255			& 245			&			\\ \hline
94		& 28			& 0--255			& 255			&			\\ \hline
\end{longtable}
\end{center}

%%%%%%%%%%%%%%%%%%%%%%%%%%%%%%%%%%%%%%%%%%%%%%%%%%%%%%%%%%%%%%%%%%%%%%%%%%%%%%%%%%%%
\section{Feedback Control (BEMF)}
\label{BEMF}\index{BEMF|see {feedback control}}\index{feedback control}

Feedback control---sometimes mistakenly called `BEMF'---is a method for regulating a motor's speed using a feedback loop. The motor speed is continuously monitored, and compared to the desired speed; the applied voltage is adjusted up or down to bring the monitored speed to the desired speed as quickly as possible. Because a DC motor and a DC dynamo are essentially the same thing, the speed of a DC motor can be measured by allowing it to freewheel, and observing the generated voltage. This voltage, called back-EMF (or BEMF for short) is only one of many methods generally available to measure a DC motor's speed, but the only one available for most model trains.

The advantages of feedback control are many: The locomotive will accelerate quickly to the desired speed regardless whether it is running light or hauling a long string of cars, running uphill or downhill. Additionally, low speed performance may be improved in many cases, as feedback control can help to smoothly overcome static friction (stiction), and maintain a smooth crawl.

Many feedback algorithms exist; Aegaeon uses one called \textsc{pi+}. The \textsc{pi+} algorithm has three tunable parameters that will need adjusting to your particular motor. The defaults were chosen to give reasonable results out of the box; nevertheless, you should consider tuning them.

\index{feedback control!proportional term}The first term is called the \textit{proportional} term, and controls the speed with which the algorithm corrects errors. A value too small leads to ineffective feedback control. A value too large leads to jerky, uneven performance.

\index{configuration variable!CV 061@CV 61}
\label{CV61}
\begin{center}
\begin{tabular}{|l|c|c|c|}
\hline
\multicolumn{4}{|c|}{\textbf{CV 61 --- Feedback Control Proportional Term}} \\ \hline \hline
\textit{Feature} & \textit{Options} & \textit{Default} & \textit{User} \\ \hline
Strength & 0--255 & 50 &\\ \hline
\end{tabular}
\end{center}

\index{feedback control!integral term}The second term is called the \textit{integral} term, and helps smooth out the correction. A value too small will fail to correct for jerky, uneven performance. A value too large will result in too slow a correction in error.

\index{configuration variable!CV 062@CV 62}
\label{CV62}
\begin{center}
\begin{tabular}{|l|c|c|c|}
\hline
\multicolumn{4}{|c|}{\textbf{CV 62 --- Feedback Control Integral Term}} \\ \hline \hline
\textit{Feature} & \textit{Options} & \textit{Default} & \textit{User} \\ \hline
Strength & 0--255 & 24 &\\ \hline
\end{tabular}
\end{center}

\index{feedback control!stiffness term}\label{MotorControlInConsist}The third term is called the \textit{stiffness} term, and is used to scale the effects of the \textit{integral} term. Stiffness determines how readily the decoder overcomes sudden changes in motor speed. A large value increases the stiffness, the decoder's resistance to changes. A small value decreases the stiffness. In general, larger values of stiffness are good for running solo, but lead to fighting in consists---an unacceptable pushing and pulling against each other. For this reason, Aegaeon provides two different stiffness settings, one for use when running solo, and one automatically activated with advanced consisting (see \S\ref{AdvancedConsisting}).

\index{configuration variable!CV 063@CV 63}
\label{CV63}
\begin{center}
\begin{tabular}{|l|c|c|c|}
\hline
\multicolumn{4}{|c|}{\textbf{CV 63 --- Feedback Control Stiffness Term (Solo)}} \\ \hline \hline
\textit{Feature} & \textit{Options} & \textit{Default} & \textit{User} \\ \hline
Strength & 0--255 & 255 &\\ \hline
\end{tabular}
\end{center}

\index{configuration variable!CV 064@CV 64}
\label{CV64}
\begin{center}
\begin{tabular}{|l|c|c|c|}
\hline
\multicolumn{4}{|c|}{\textbf{CV 64 --- Feedback Control Stiffness Term (Consist)}} \\ \hline \hline
\textit{Feature} & \textit{Options} & \textit{Default} & \textit{User} \\ \hline
Strength & 0--255 & 152 &\\ \hline
\end{tabular}
\end{center}

\label{FeedbackActivation}\index{feedback control!activation}Two more settings are available to tune the feedback control performance. The Feedback Cutout determines the speed (in 128-speed steps) at or above which the feedback control algorithm is shut off. This is useful if you only wish to use feedback control for low speed operations, or find that you prefer the non-feedback controlled performance at higher speeds. A value of 0 turns feedback control off entirely. A value of, for example, 10 turns feedback control off at speed step 10 and above. A value of 126 activates it for all speeds.

If you are using 28-speed step control, you will have to calculate the proper value; the cut off value will be 4.5 times the 28-step speed step.

\index{configuration variable!CV 010@CV 10}
\label{CV10}
\begin{center}
\begin{tabular}{|l|c|c|c|}
\hline
\multicolumn{4}{|c|}{\textbf{CV 10 --- Feedback Control Cutout}} \\ \hline \hline
\textit{Feature} & \textit{Options} & \textit{Default} & \textit{User} \\ \hline
Speed & 0--127 & 0 &\\ \hline
\end{tabular}
\end{center}

\index{feedback control!sampling frequency}The feedback control must shut off the control voltage to the motor to measure the BEMF. For this reason, continuous sampling is impossible. Rather, the feedback controller takes samples at a fixed interval. This interval, specified in milliseconds, is adjustable. Setting the value too low will reduce the available torque; setting it too high will result in slow response to changing conditions. Setting the value below approximately 10ms, however, results in undefined behavior and is strongly recommended against.

\index{configuration variable!CV 060@CV 60}
\label{CV60}
\begin{center}
\begin{tabular}{|l|c|c|c|}
\hline
\multicolumn{4}{|c|}{\textbf{CV 60 --- Feedback Sampling Interval}} \\ \hline \hline
\textit{Feature} & \textit{Options} & \textit{Default} & \textit{User} \\ \hline
Interval in ms & 10--255 & 100 &\\ \hline
\end{tabular}
\end{center}

\subsection{Tuning the Feedback Control Parameters}

There is a specific method that should be employed for tuning the feedback control terms in CV 61--64.
% TODO write that method

\section{Shunting Mode}
\label{ShuntingMode}

Shunting mode allows you finer control over low speed operations, such as in a yard, by halving the motor speed. By default, Function 5 is used to trigger shunting mode. See \S\ref{remapping} for the settings that permit you to reassign this functionality to a different function button.

%%%%%%%%%%%%%%%%%%%%%%%%%%%%%%%%%%%%%%%%%%%%%%%%%%%%%%%%%%%%%%%%%%%%%%%%%%%%%%%%%%%%
%%%%%%%%%%%%%%%%%%%%%%%%%%%%%%%%%%%%%%%%%%%%%%%%%%%%%%%%%%%%%%%%%%%%%%%%%%%%%%%%%%%%
%%%%%%%%%%%%%%%%%%%%%%%%%%%%%%%%%%%%%%%%%%%%%%%%%%%%%%%%%%%%%%%%%%%%%%%%%%%%%%%%%%%%
\chapter{Special Effects Configuration}
\label{specialeffectsconfiguration}
This chapter applies mainly to the Aegaeon:L2 and :C decoders, although it also covers the special Shunting Mode available on the Aegaeon:M.

The Aegaeon:L2 and :C decoders provide a pair of highly configurable lighting outputs. The lighting outputs can be used to drive LEDs or bulbs. Each lighting output has the following options available:
\begin{itemize}
\item Configurable full brightness
\item Configurable directionality (on forwards, on reverse, on both, on neither)
\item Rule 17 dimming, with any combination of:
\begin{itemize}
\item Dim in reverse
\item Dim in forward
\item Dim when stopped
\item Dim on command
\end{itemize}
\item Configurable Rule 17 (dimmed) brightness
\item Optional simulated soft-start effect
\item Animations, with configurable time duration:
\begin{itemize}
\item strobe
\item double strobe
\item rotary beacon
\item firebox / random flicker
\item Mars light
\item Gyra light
\item Left and right ditch lights
\end{itemize}
\item Animations can be set to always-on, or triggered on command
\end{itemize}

\section{Outputs and Functions}
\index{functions}\index{outputs}

First, let us draw a distinction between \textit{Outputs} and \textit{Functions}.

Most decoders, Aegaeon included, provide one or more \textit{Outputs} for controlling special effects. In most cases, these outputs will have physical representation in the form of function wires on the decoder. Sometimes, however, the Output will be tied to a purely logical representation, internal to the operation of the decoder. The Outputs on Aegaeon are numbered from 1 to 7 (see \S\ref{outputs} below).

Functions, on the other hand, are messages sent by a throttle in response to button presses. The buttons on a throttle are labeled from 0 to 10 or perhaps as high as 28. The NMRA defines a default mapping of Functions to Outputs (see \S\ref{remapping} for details), while also providing a mechanism for remapping the Function-to-Output connections, at least within certain bounds.

\section{Decoder Outputs}
\label{outputs}

Most of the special effects configuration options adjust the behavior of Outputs (as opposed to Functions). Aegaeon:L2 and :C provide for seven distinct Outputs, each of which can be assigned to a range of function buttons (see \S\ref{remapping} for details on how to do this).

\begin{center}
\begin{tabular}{|c|r|}
\hline
Output 1 & white wire \\ \hline
Output 2 & yellow wire \\ \hline
Output 3 & white wire animation \\ \hline
Output 4 & yellow wire animation \\ \hline
Output 5 & white wire Rule 17 dimming \\ \hline
Output 6 & yellow wire Rule 17 dimming \\ \hline
Output 7 & shunting mode (:L2 only) (see \S\ref{ShuntingMode})\\ \hline
\end{tabular}
\end{center}

Notice that on Aegaeon:L2, ``white wire'' above means that the output attached to the white wire will be activated. On Aegaeon:C, it means that the white wire is made positive relative to the yellow wire.

Aegaeon:M provides a much more limited range of Outputs:

\begin{center}
\begin{tabular}{|c|r|}
\hline
Output 1 & (no connection) \\ \hline
Output 2 & (no connection) \\ \hline
Output 3 & (no connection) \\ \hline
Output 4 & (no connection) \\ \hline
Output 5 & (no connection) \\ \hline
Output 6 & (no connection) \\ \hline
Output 7 & shunting mode (see \S\ref{ShuntingMode})\\ \hline
\end{tabular}
\end{center}

\section{Lighting Brightness}

The brightness for each of the two lighting outputs (Outputs 1 and 2) can be controlled independently. In addition, the dimmed or Rule 17 brightness for each output can be set as well (see \S\ref{Rule17} for more details on Rule 17 dimming).

\index{configuration variable!CV 049@CV 49}\index{lighting!setting the brightness of}
\label{CV49}
\begin{center}
\begin{tabular}{|l|c|c|c|}
\hline
\multicolumn{4}{|c|}{\textbf{CV 49 --- Output 1 Full Brightness}} \\ \hline \hline
\textit{Feature} & \textit{Options} & \textit{Default} & \textit{User} \\ \hline
Brightness & 0--255 & 255 &\\ \hline
\end{tabular}
\end{center}

\index{configuration variable!CV 050@CV 50}
\label{CV50}
\begin{center}
\begin{tabular}{|l|c|c|c|}
\hline
\multicolumn{4}{|c|}{\textbf{CV 50 --- Output 1 Dimmed Brightness}} \\ \hline \hline
\textit{Feature} & \textit{Options} & \textit{Default} & \textit{User} \\ \hline
Brightness & 0--255 & 255 &\\ \hline
\end{tabular}
\end{center}

\index{configuration variable!CV 054@CV 54}
\label{CV54}
\begin{center}
\begin{tabular}{|l|c|c|c|}
\hline
\multicolumn{4}{|c|}{\textbf{CV 54 --- Output 2 Full Brightness}} \\ \hline \hline
\textit{Feature} & \textit{Options} & \textit{Default} & \textit{User} \\ \hline
Brightness & 0--255 & 255 &\\ \hline
\end{tabular}
\end{center}

\index{configuration variable!CV 055@CV 55}
\label{CV55}
\begin{center}
\begin{tabular}{|l|c|c|c|}
\hline
\multicolumn{4}{|c|}{\textbf{CV 55 --- Output 2 Dimmed Brightness}} \\ \hline \hline
\textit{Feature} & \textit{Options} & \textit{Default} & \textit{User} \\ \hline
Brightness & 0--255 & 255 &\\ \hline
\end{tabular}
\end{center}

\section{Lighting Directionality, Rule 17, and Soft Start}

Each of the two lighting outputs (Outputs 1 and 2) can be set to turn on and off automatically with the direction of the train. The lights can also always be controlled with function buttons. (Both lights by default map to Function 0, sometimes called Function L; see \S\ref{remapping} for more details.)

\label{configRule17}Additionally, each output can be configured to dim under certain circumstances: when the locomotive is moving forwards, when the locomotive is moving in reverse, or when the locomotive is stopped. Rule 17 dimming can always be activated through Outputs 5 and 6 ((which by default map to Functions 3 and 4). For more on Rule 17 dimming, what it is, and how you might use it in your models, see \S\ref{Rule17}.

\label{configSoftStart}\index{lighting!soft start}Finally, each output can be configured to simulate the presence of a soft start device. Soft start devices limit the current drawn by a real locomotive's headlight, and hence yield a slow, smooth ramping of the bulb's brightness. This effect can be simulated by setting the option below.

\index{configuration variable!CV 048@CV 48}
\label{CV48}
\begin{center}
\begin{tabular}{|l|lc|c|c|}
\hline
\multicolumn{5}{|c|}{\textbf{CV 48 --- Directionality, Rule 17 Dimming,}} \\
\multicolumn{5}{|c|}{\textbf{and Soft start for Output 1}} \\ \hline \hline
\textit{Feature} & \multicolumn{2}{c|}{\textit{Options}} & \textit{Default} & \textit{User} \\ \hline
\multirow{2}{*}{On Forward}	& \textbf{On}	& \textbf{1} 	& \multirow{2}{*}{1} 	&\\
			& Off 		& 0 			& 				& \\ \hline
\multirow{2}{*}{On Reverse}	& On			& 2 			& \multirow{2}{*}{0} 	&\\
			& \textbf{Off} 	& \textbf{0} 	& 				& \\ \hline
\multirow{2}{*}{Dim Forward Stopped}	& On			& 4 			& \multirow{2}{*}{0} 	&\\
			& \textbf{Off} 	& \textbf{0} 	& 				& \\ \hline
\multirow{2}{*}{Dim Reverse Stopped}	& On			& 8 			& \multirow{2}{*}{0} 	&\\
			& \textbf{Off} 	& \textbf{0} 	& 				& \\ \hline
\multirow{2}{*}{Dim Forward}	& On			& 16 			& \multirow{2}{*}{0} 	&\\
			& \textbf{Off} 	& \textbf{0} 	& 				& \\ \hline
\multirow{2}{*}{Dim Reverse}	& On			& 32 			& \multirow{2}{*}{0} 	&\\
			& \textbf{Off} 	& \textbf{0} 	& 				& \\ \hline
\multirow{2}{*}{Soft Start Effect}	& On			& 64 			& \multirow{2}{*}{0} 	&\\
			& \textbf{Off} 	& \textbf{0} 	& 				& \\ \hline\hline
\multicolumn{3}{|r|}{\textit{Total}} & 1 &\\ \hline
\end{tabular}
\end{center}

\index{configuration variable!CV 053@CV 53}
\label{CV53}
\begin{center}
\begin{tabular}{|l|lc|c|c|}
\hline
\multicolumn{5}{|c|}{\textbf{CV 53 --- Directionality, Rule 17 Dimming,}} \\
\multicolumn{5}{|c|}{\textbf{and Soft start for Output 2}} \\ \hline \hline
\textit{Feature} & \multicolumn{2}{c|}{\textit{Options}} & \textit{Default} & \textit{User} \\ \hline
\multirow{2}{*}{On Forward}	& On			& 1 	& \multirow{2}{*}{0} 	&\\
			& \textbf{Off} 	& \textbf{0} 			& 				& \\ \hline
\multirow{2}{*}{On Reverse}	& \textbf{On}	& \textbf{2} 			& \multirow{2}{*}{2} 	&\\
			& Off 		& 0 	& 	& \\ \hline
\multirow{2}{*}{Dim Forward Stopped}		& On		& 4 			& \multirow{2}{*}{0} 	&\\
			& \textbf{Off} 	& \textbf{0} 	& 				& \\ \hline
\multirow{2}{*}{Dim Reverse Stopped}		& On			& 8 			& \multirow{2}{*}{0} 	&\\
			& \textbf{Off} 	& \textbf{0} 	& 				& \\ \hline
\multirow{2}{*}{Dim Forward}	& On			& 16 			& \multirow{2}{*}{0} 	&\\
			& \textbf{Off} 	& \textbf{0} 	& 				& \\ \hline
\multirow{2}{*}{Dim Reverse}	& On			& 32 			& \multirow{2}{*}{0} 	&\\
			& \textbf{Off} 	& \textbf{0} 	& 				& \\ \hline
\multirow{2}{*}{Soft Start Effect}	& On			& 64 			& \multirow{2}{*}{0} 	&\\
			& \textbf{Off} 	& \textbf{0} 	& 				& \\ \hline\hline

\multicolumn{3}{|r|}{\textit{Total}} & 2 &\\ \hline
\end{tabular}
\end{center}

\section{Lighting Animations}

Each of the two outputs can be optionally assigned an animation designed to simulate some physical device such as a strobe or firebox. Furthermore, these animations can be static (on whenever the lighting output is on), or trigged by a function button such that the output alternates between steady on and animated, depending on the push of a button. This is particularly useful in the case of ditch lights and Mars or Gyra lights, which the engineer has the option of turning on and off independently of the light itself. The choice of animation and whether that animation is triggerable is controlled by Output Animation (CV 51 and 56). The animation triggers are on Outputs 3 and 4 (which by default map to Functions 1 and 2).

The speed of each output's animations can also be adjusted. Each animation comprises 64 frames; by default, each frame lasts 62ms, giving a total animation period of 2 seconds. If you find the animations to be too fast or too slow, you can adjust the Animation Period (CV 52 and 57) settings.

The animations on both lighting Outputs are designed to work in sync, so that for example the left and right ditch lights will always flash in opposition. If you find this synchronization unwelcome, consider adjusting one or both of the Animation Periods (CV 52 and 57) to pull them out of sync.

Not sure what a Gyra Light is? What use is a random flicker? To learn more about prototypical uses for the animations, turn to \S\ref{animations}

\index{configuration variable!CV 051@CV 51}
\label{CV51}
\begin{center}
\begin{tabular}{|l|lc|c|c|}
\hline
\multicolumn{5}{|c|}{\textbf{CV 51 --- Output 1 Animation}} \\ \hline \hline
\textit{Feature} & \multicolumn{2}{c|}{\textit{Options}} & \textit{Default} & \textit{User} \\ \hline
\multirow{9}{*}{Animation}		& \textbf{Off}		& \textbf{0} 		& \multirow{9}{*}{0} 	&\\
			& Strobe 			& 1 		& 				& \\ 
			& Double Strobe	& 2 		& 				& \\ 
			& Rotary Beacon 	& 3 		& 				& \\ 
			& Firebox / Random Flicker 			& 4 		& 				& \\ 
			& Left Ditch Light 	& 5 		& 				& \\ 
			& Right Ditch Light 	& 6 		& 				& \\
			& Mars Light 		& 7 		& 				& \\
			& Gyra Light 		& 8 		& 				& \\ \hline
\multirow{2}{*}{Triggerable}	& \textbf{No}		& \textbf{0} 		& \multirow{2}{*}{0} 	&\\
			& Yes	 		& 128	& 				& \\ \hline\hline
\multicolumn{3}{|r|}{\textit{Total}} & 0 &\\ \hline
\end{tabular}
\end{center}

\index{configuration variable!CV 052@CV 52}
\label{CV52}
\begin{center}
\begin{tabular}{|l|c|c|c|}
\hline
\multicolumn{4}{|c|}{\textbf{CV 52 --- Output 1 Animation Period}} \\ \hline \hline
\textit{Feature} & \textit{Options} & \textit{Default} & \textit{User} \\ \hline
Period in ms & 0--255 & 62 &\\ \hline
\end{tabular}
\end{center}

\index{configuration variable!CV 056@CV 56}
\label{CV56}
\begin{center}
\begin{tabular}{|l|lc|c|c|}
\hline
\multicolumn{5}{|c|}{\textbf{CV 56 --- Output 2 Animation}} \\ \hline \hline
\textit{Feature} & \multicolumn{2}{c|}{\textit{Options}} & \textit{Default} & \textit{User} \\ \hline
\multirow{9}{*}{Animation}		& \textbf{Off}		& \textbf{0} 		& \multirow{9}{*}{0} 	&\\
			& Strobe 			& 1 		& 				& \\ 
			& Double Strobe	& 2 		& 				& \\ 
			& Rotary Beacon 	& 3 		& 				& \\ 
			& Firebox / Random Flicker 			& 4 		& 				& \\ 
			& Left Ditch Light 	& 5 		& 				& \\ 
			& Right Ditch Light 	& 6 		& 				& \\
			& Mars Light 		& 7 		& 				& \\
			& Gyra Light 		& 8 		& 				& \\ \hline
\multirow{2}{*}{Triggerable}	& \textbf{No}		& \textbf{0} 		& \multirow{2}{*}{0} 	&\\
			& Yes	 		& 128	& 				& \\ \hline\hline
\multicolumn{3}{|r|}{\textit{Total}} & 0 &\\ \hline
\end{tabular}
\end{center}

\index{configuration variable!CV 057@CV 57}
\label{CV57}
\begin{center}
\begin{tabular}{|l|c|c|c|}
\hline
\multicolumn{4}{|c|}{\textbf{CV 57 --- Output 2 Animation Period}} \\ \hline \hline
\textit{Feature} & \textit{Options} & \textit{Default} & \textit{User} \\ \hline
Period in ms & 0--255 & 62 &\\ \hline
\end{tabular}
\end{center}

\section{Function Control of Lighting}

Aegaeon offers a highly flexible system for configuring how the lighting and other special effects are triggered. You can customize which function buttons on your thorttle operate the lighting, how the lighting operations behave when in an Advanced Consist, and how they behave when running on DC (and hence beyond the reach of the function buttons on your DCC throttle).

\subsection{Mapping Functions to Outputs}
\label{remapping}\index{lighting!mapping to functions}\index{function mapping}

Each of the seven Outputs provided by Aegaeon are mapped to the Function buttons on your throttle as below. If this mapping does not suit, it can be adjusted to better fit your desired operating scheme.

\begin{center}
\begin{tabular}{|c|c|c|c|}
\hline
\textit{Output} & \textit{Description} & \textit{Default} & \textit{Available} \\ \hline
1 & white wire & F0 (FL) & F0--F3 \\ \hline
2 & yellow wire & F0 (FL) & F0--F3\\ \hline
3 &  white wire animation trigger & F1 & F0--F3\\ \hline
4 & yellow wire animation trigger & F2 & F0--F8\\ \hline
5 & white wire Rule 17 dimming & F3 & F0--F8\\ \hline
6 & yellow wire Rule 17 dimming & F4 & F0--F8\\ \hline
7 & shunting mode & F5 & F0--F8\\ \hline
\end{tabular}
\end{center}

(If you are wondering why Outputs 1, 2, and 3 can only be mapped to a much smaller range than the rest, blame the NMRA; this was not our decision to make.)

Each Function button can be assigned to trigger zero or more Outputs. The procedure for doing this is as follows. For each Function buttons, decide which Outputs (perhaps more than one) that that Function should trigger, locate the appropriate CV tables below, and add up the rows for the selected Outputs to determine the value to program to that CV.

Bear in mind that only the :L2 supports all seven Outputs. See \S\ref{outputs} for details.

(The astute will observe that many decoders, and indeed the NMRA specifications for function remapping, draw a distinction between F0 when running forwards and when running backwards, as though these were two distinct Functions. In fact, they are not, and the Aegaeon family of decoders does not recognize this distinction. Thus, Aegaeon uses only CV 34 to remap F0, and ignores CV 33. If you are not sure what this means, or why we raise this issue, then you might be happier if you ignored this parenthetical note.)

\index{configuration variable!CV 034@CV 34}
\label{CV34}
\begin{center}
\begin{tabular}{|l|lc|c|c|}
\hline
\multicolumn{5}{|c|}{\textbf{CV 34 --- F0 Output Mapping}} \\ \hline \hline
\textit{Feature} & \multicolumn{2}{c|}{\textit{Options}} & \textit{Default} & \textit{User} \\ \hline
\multirow{2}{*}{White Wire} & Not Mapped to F0 & 0	& 	\multirow{2}{*}{1}&\\
                             & \textbf{Mapped to F0} & \textbf{1} & & \\ \hline
\multirow{2}{*}{Yellow Wire} & Not Mapped to F0 & 0	& 	\multirow{2}{*}{2}&\\
                             & \textbf{Mapped to F0} & \textbf{2} & & \\ \hline
\multirow{2}{*}{White Wire Animation Trigger} & \textbf{Not Mapped to F0} & \textbf{0}	& 	\multirow{2}{*}{0}& \\
                             & Mapped to F0 & 4 & & \\ \hline
\multirow{2}{*}{Yellow Wire Animation Trigger} & \textbf{Not Mapped to F0} & \textbf{0}	& 	\multirow{2}{*}{0}&\\
                             & Mapped to F0 & 8 & & \\ \hline
\multirow{2}{*}{White Wire Rule 17 Dimming} & \textbf{Not Mapped to F0} & \textbf{0}	& 	\multirow{2}{*}{0}& \\
                             & Mapped to F0 & 16 & & \\ \hline
\multirow{2}{*}{Yellow Wire Rule 17 Dimming} & \textbf{Not Mapped to F0} & \textbf{0}	& 	\multirow{2}{*}{0}& \\
                             & Mapped to F0 & 32 & & \\ \hline
\multirow{2}{*}{Shunting Mode}  & \textbf{Not Mapped to F0} & \textbf{0}	& 	\multirow{2}{*}{0}&\\
                             & Mapped to F0 & 64 & & \\ \hline\hline
\multicolumn{3}{|r|}{\textit{Total}} & 3 &\\ \hline
\end{tabular}
\end{center}

\index{configuration variable!CV 035@CV 35}
\label{CV35}
\begin{center}
\begin{tabular}{|l|lc|c|c|}
\hline
\multicolumn{5}{|c|}{\textbf{CV 35 --- F1 Output Mapping}} \\ \hline \hline
\textit{Feature} & \multicolumn{2}{c|}{\textit{Options}} & \textit{Default} & \textit{User} \\ \hline
\multirow{2}{*}{White Wire} & \textbf{Not Mapped to F1} & \textbf{0}	& 	\multirow{2}{*}{0}&\\
                            & Mapped to F1 & 1 & & \\ \hline
\multirow{2}{*}{Yellow Wire} & \textbf{Not Mapped to F1} & \textbf{0}	& 	\multirow{2}{*}{0}&\\
                            & Mapped to F1 & 2 & & \\ \hline
\multirow{2}{*}{White Wire Animation Trigger} & Not Mapped to F1 & 0	& 	\multirow{2}{*}{4}& \\
                           & \textbf{Mapped to F1} & \textbf{4} & & \\ \hline
\multirow{2}{*}{Yellow Wire Animation Trigger} & \textbf{Not Mapped to F1} & \textbf{0}	& 	\multirow{2}{*}{0}&\\
                             & Mapped to F1 & 8 & & \\ \hline
\multirow{2}{*}{White Wire Rule 17 Dimming} & \textbf{Not Mapped to F1} & \textbf{0}	& 	\multirow{2}{*}{0}& \\
                             & Mapped to F1 & 16 & & \\ \hline
\multirow{2}{*}{Yellow Wire Rule 17 Dimming} & \textbf{Not Mapped to F1} & \textbf{0}	& 	\multirow{2}{*}{0}& \\
                           & Mapped to F1 & 32 & & \\ \hline
\multirow{2}{*}{Shunting Mode} & \textbf{Not Mapped to F1} & \textbf{0}	& 	\multirow{2}{*}{0}&\\
                             & Mapped to F1 & 64 & & \\ \hline\hline
\multicolumn{3}{|r|}{\textit{Total}} & 4 &\\ \hline
\end{tabular}
\end{center}

\index{configuration variable!CV 036@CV 36}
\label{CV36}
\begin{center}
\begin{tabular}{|l|lc|c|c|}
\hline
\multicolumn{5}{|c|}{\textbf{CV 36 --- F2 Output Mapping}} \\ \hline \hline
\textit{Feature} & \multicolumn{2}{c|}{\textit{Options}} & \textit{Default} & \textit{User} \\ \hline
\multirow{2}{*}{White Wire} & \textbf{Not Mapped to F2} & \textbf{0}	& 	\multirow{2}{*}{0}&\\
                            & Mapped to F2 & 1 & & \\ \hline
\multirow{2}{*}{Yellow Wire} & \textbf{Not Mapped to F2} & \textbf{0}	& 	\multirow{2}{*}{0}&\\
                            & Mapped to F2 & 2 & & \\ \hline
\multirow{2}{*}{White Wire Animation Trigger} & \textbf{Not Mapped to F2} & \textbf{0}	& 	\multirow{2}{*}{0}& \\
                           & Mapped to F2 & 4 & & \\ \hline
\multirow{2}{*}{Yellow Wire Animation Trigger} & Not Mapped to F2 & 0	& 	\multirow{2}{*}{8}& \\
                           & \textbf{Mapped to F2} & \textbf{8} & & \\ \hline
\multirow{2}{*}{White Wire Rule 17 Dimming} & \textbf{Not Mapped to F2} & \textbf{0}	& 	\multirow{2}{*}{0}& \\
                             & Mapped to F2 & 16 & & \\ \hline
\multirow{2}{*}{Yellow Wire Rule 17 Dimming} & \textbf{Not Mapped to F2} & \textbf{0}	& 	\multirow{2}{*}{0}&\\
                             & Mapped to F2 & 32 & & \\ \hline
\multirow{2}{*}{Shunting Mode} & \textbf{Not Mapped to F2} & \textbf{0}	& 	\multirow{2}{*}{0}&\\
                             & Mapped to F2 & 64 & & \\ \hline\hline
\multicolumn{3}{|r|}{\textit{Total}} & 8 &\\ \hline
\end{tabular}
\end{center}

\index{configuration variable!CV 037@CV 37}
\label{CV37}
\begin{center}
\begin{tabular}{|l|lc|c|c|}
\hline
\multicolumn{5}{|c|}{\textbf{CV 37 --- F3 Output Mapping}} \\ \hline \hline
\textit{Feature} & \multicolumn{2}{c|}{\textit{Options}} & \textit{Default} & \textit{User} \\ \hline
\multirow{2}{*}{White Wire} & \textbf{Not Mapped to F3} & \textbf{0}	& 	\multirow{2}{*}{0}&\\
                            & Mapped to F3 & 1 & & \\ \hline
\multirow{2}{*}{Yellow Wire} & \textbf{Not Mapped to F3} & \textbf{0}	& 	\multirow{2}{*}{0}&\\
                            & Mapped to F3 & 2 & & \\ \hline
\multirow{2}{*}{White Wire Animation Trigger} & \textbf{Not Mapped to F3} & \textbf{0}	& 	\multirow{2}{*}{0}& \\
                           & Mapped to F3 & 4 & & \\ \hline
\multirow{2}{*}{Yellow Wire Animation Trigger} & \textbf{Not Mapped to F3} & \textbf{0}	& 	\multirow{2}{*}{0}& \\
                           & Mapped to F3 & 8 & & \\ \hline
\multirow{2}{*}{White Wire Rule 17 Dimming} & Not Mapped to F3 & 0	& 	\multirow{2}{*}{16}& \\
                             & \textbf{Mapped to F3} & \textbf{16} & & \\ \hline
\multirow{2}{*}{Yellow Wire Rule 17 Dimming} & \textbf{Not Mapped to F3} & \textbf{0}	& 	\multirow{2}{*}{0}&\\
                             & Mapped to F3 & 32 & & \\ \hline
\multirow{2}{*}{Shunting Mode} & \textbf{Not Mapped to F3} & \textbf{0}	& 	\multirow{2}{*}{0}&\\
                             & Mapped to F3 & 64 & & \\ \hline\hline
\multicolumn{3}{|r|}{\textit{Total}} & 16 &\\ \hline
\end{tabular}
\end{center}

\index{configuration variable!CV 038@CV 38}
\label{CV38}
\begin{center}
\begin{tabular}{|l|lc|c|c|}
\hline
\multicolumn{5}{|c|}{\textbf{CV 38 --- F4 Output Mapping}} \\ \hline \hline
\textit{Feature} & \multicolumn{2}{c|}{\textit{Options}} & \textit{Default} & \textit{User} \\ \hline
\multirow{2}{*}{Yellow Wire Animation Trigger} & \textbf{Not Mapped to F4} & \textbf{0}	& 	\multirow{2}{*}{0}& \\
                           & Mapped to F4 & 1 & & \\ \hline
\multirow{2}{*}{White Wire Rule 17 Dimming} & \textbf{Not Mapped to F4} & \textbf{0}	& 	\multirow{2}{*}{0}& \\
                             & Mapped to F4 & 2 & & \\ \hline
\multirow{2}{*}{Yellow Wire Rule 17 Dimming} & Not Mapped to F4 & 0	& 	\multirow{2}{*}{4}&\\
                             & \textbf{Mapped to F4} & \textbf{4} & & \\ \hline
\multirow{2}{*}{Shunting Mode} & \textbf{Not Mapped to F4} & \textbf{0}	& 	\multirow{2}{*}{0}&\\
                             & Mapped to F4 & 8 & & \\ \hline\hline
\multicolumn{3}{|r|}{\textit{Total}} & 4 &\\ \hline
\end{tabular}
\end{center}

\index{configuration variable!CV 039@CV 39}
\label{CV39}
\begin{center}
\begin{tabular}{|l|lc|c|c|}
\hline
\multicolumn{5}{|c|}{\textbf{CV 39 --- F5 Output Mapping}} \\ \hline \hline
\textit{Feature} & \multicolumn{2}{c|}{\textit{Options}} & \textit{Default} & \textit{User} \\ \hline
\multirow{2}{*}{Yellow Wire Animation Trigger} & \textbf{Not Mapped to F5} & \textbf{0}	& 	\multirow{2}{*}{0}& \\
                           & Mapped to F5 & 1 & & \\ \hline
\multirow{2}{*}{White Wire Rule 17 Dimming} & \textbf{Not Mapped to F5} & \textbf{0}	& 	\multirow{2}{*}{0}& \\
                             & Mapped to F5 & 2 & & \\ \hline
\multirow{2}{*}{Yellow Wire Rule 17 Dimming} & \textbf{Not Mapped to F5} & \textbf{0}	& 	\multirow{2}{*}{0}&\\
                             & Mapped to F5 & 4 & & \\ \hline
\multirow{2}{*}{Shunting Mode} & Not Mapped to F5 & 0	& 	\multirow{2}{*}{8}&\\
                             & \textbf{Mapped to F5} & \textbf{8} & & \\ \hline\hline
\multicolumn{3}{|r|}{\textit{Total}} & 8 &\\ \hline
\end{tabular}
\end{center}

\index{configuration variable!CV 040@CV 40}
\label{CV40}
\begin{center}
\begin{tabular}{|l|lc|c|c|}
\hline
\multicolumn{5}{|c|}{\textbf{CV 40 --- F6 Output Mapping}} \\ \hline \hline
\textit{Feature} & \multicolumn{2}{c|}{\textit{Options}} & \textit{Default} & \textit{User} \\ \hline
\multirow{2}{*}{Yellow Wire Animation Trigger} & \textbf{Not Mapped to F6} & \textbf{0}	& 	\multirow{2}{*}{0}& \\
                           & Mapped to F6 & 1 & & \\ \hline
\multirow{2}{*}{White Wire Rule 17 Dimming} & \textbf{Not Mapped to F6} & \textbf{0}	& 	\multirow{2}{*}{0}& \\
                             & Mapped to F6 & 2 & & \\ \hline
\multirow{2}{*}{Yellow Wire Rule 17 Dimming} & \textbf{Not Mapped to F6} & \textbf{0}	& 	\multirow{2}{*}{0}&\\
                             & Mapped to F6 & 4 & & \\ \hline
\multirow{2}{*}{Shunting Mode} & \textbf{Not Mapped to F6} & \textbf{0}	& 	\multirow{2}{*}{0}&\\
                             & Mapped to F6 & 8 & & \\ \hline\hline
\multicolumn{3}{|r|}{\textit{Total}} & 0 &\\ \hline
\end{tabular}
\end{center}

\index{configuration variable!CV 041@CV 41}
\label{CV41}
\begin{center}
\begin{tabular}{|l|lc|c|c|}
\hline
\multicolumn{5}{|c|}{\textbf{CV 41 --- F7 Output Mapping}} \\ \hline \hline
\textit{Feature} & \multicolumn{2}{c|}{\textit{Options}} & \textit{Default} & \textit{User} \\ \hline
\multirow{2}{*}{Yellow Wire Animation Trigger} & \textbf{Not Mapped to F7} & \textbf{0}	& 	\multirow{2}{*}{0}& \\
                           & Mapped to F7 & 1 & & \\ \hline
\multirow{2}{*}{White Wire Rule 17 Dimming} & \textbf{Not Mapped to F7} & \textbf{0}	& 	\multirow{2}{*}{0}& \\
                             & Mapped to F7 & 2 & & \\ \hline
\multirow{2}{*}{Yellow Wire Rule 17 Dimming} & \textbf{Not Mapped to F7} & \textbf{0}	& 	\multirow{2}{*}{0}&\\
                             & Mapped to F7 & 4 & & \\ \hline
\multirow{2}{*}{Shunting Mode} & \textbf{Not Mapped to F7} & \textbf{0}	& 	\multirow{2}{*}{0}&\\
                             & Mapped to F7 & 8 & & \\ \hline\hline
\multicolumn{3}{|r|}{\textit{Total}} & 0 &\\ \hline
\end{tabular}
\end{center}

\index{configuration variable!CV 042@CV 42}
\label{CV42}
\begin{center}
\begin{tabular}{|l|lc|c|c|}
\hline
\multicolumn{5}{|c|}{\textbf{CV 42 --- F8 Output Mapping}} \\ \hline \hline
\textit{Feature} & \multicolumn{2}{c|}{\textit{Options}} & \textit{Default} & \textit{User} \\ \hline
\multirow{2}{*}{Yellow Wire Animation Trigger} & \textbf{Not Mapped to F8} & \textbf{0}	& 	\multirow{2}{*}{0}& \\
                           & Mapped to F8 & 1 & & \\ \hline
\multirow{2}{*}{White Wire Rule 17 Dimming} & \textbf{Not Mapped to F8} & \textbf{0}	& 	\multirow{2}{*}{0}& \\
                             & Mapped to F8 & 2 & & \\ \hline
\multirow{2}{*}{Yellow Wire Rule 17 Dimming} & \textbf{Not Mapped to F8} & \textbf{0}	& 	\multirow{2}{*}{0}&\\
                             & Mapped to F8 & 4 & & \\ \hline
\multirow{2}{*}{Shunting Mode} & \textbf{Not Mapped to F8} & \textbf{0}	& 	\multirow{2}{*}{0}&\\
                             & Mapped to F8 & 8 & & \\ \hline\hline
\multicolumn{3}{|r|}{\textit{Total}} & 0 &\\ \hline
\end{tabular}
\end{center}

\subsection{Assigning Functions to an Advanced Consist}
\label{LightingInConsist}
When part of an Advanced Consist (see \S\ref{AdvancedConsisting}), the various Functions can only be controlled from the decoder's Primary Address. Sometimes, however, you would prefer to control certain Functions from the Advanced Consist Address. You can set this up with Consist Function Control. A Function under control of the Consist Address cannot be controlled from the Primary Address, and \textit{vice versa}.

\index{configuration variable!CV 021@CV 21}
\label{CV21}
\begin{center}
\begin{tabular}{|l|lc|c|c|}
\hline
\multicolumn{5}{|c|}{\textbf{CV 21 --- Consist Control of F1--F8}} \\ \hline \hline
\textit{Feature} & \multicolumn{2}{c|}{\textit{Options}} & \textit{Default} & \textit{User} \\ \hline
\multirow{2}{*}{F1} & \textbf{Primary Address Control} & \textbf{0}	& 	\multirow{2}{*}{0}& \\
                           & Consist Address Control & 1 & & \\ \hline
\multirow{2}{*}{F2} & \textbf{Primary Address Control} & \textbf{0}	& 	\multirow{2}{*}{0}& \\
                           & Consist Address Control & 2 & & \\ \hline
\multirow{2}{*}{F3} & \textbf{Primary Address Control} & \textbf{0}	& 	\multirow{2}{*}{0}& \\
                           & Consist Address Control & 4 & & \\ \hline
\multirow{2}{*}{F4} & \textbf{Primary Address Control} & \textbf{0}	& 	\multirow{2}{*}{0}& \\
                           & Consist Address Control & 8 & & \\ \hline
\multirow{2}{*}{F5} & \textbf{Primary Address Control} & \textbf{0}	& 	\multirow{2}{*}{0}& \\
                           & Consist Address Control & 16 & & \\ \hline
\multirow{2}{*}{F6} & \textbf{Primary Address Control} & \textbf{0}	& 	\multirow{2}{*}{0}& \\
                           & Consist Address Control & 32 & & \\ \hline
\multirow{2}{*}{F7} & \textbf{Primary Address Control} & \textbf{0}	& 	\multirow{2}{*}{0}& \\
                           & Consist Address Control & 64 & & \\ \hline
\multirow{2}{*}{F8} & \textbf{Primary Address Control} & \textbf{0}	& 	\multirow{2}{*}{0}& \\
                           & Consist Address Control & 128 & & \\ \hline\hline
\multicolumn{3}{|r|}{\textit{Total}} & 0 &\\ \hline
\end{tabular}
\end{center}

\index{configuration variable!CV 022@CV 22}
\label{CV22}
\begin{center}
\begin{tabular}{|l|lc|c|c|}
\hline
\multicolumn{5}{|c|}{\textbf{CV 22 --- Consist Control of F0}} \\ \hline \hline
\textit{Feature} & \multicolumn{2}{c|}{\textit{Options}} & \textit{Default} & \textit{User} \\ \hline
\multirow{2}{*}{F0} & \textbf{Primary Address Control} & \textbf{0}	& 	\multirow{2}{*}{0}& \\
                           & Consist Address Control & 1 & & \\ \hline\hline
\multicolumn{3}{|r|}{\textit{Total}} & 0 &\\ \hline
\end{tabular}
\end{center}

\subsection{Function Status in DC Mode}

When running your train with analog DC, you cannot control the lighting functions using the function keys on your throttle. Aegaeon allows you to set up the default Function behaviors when running on DC. Functions can be set to turn off when running on DC (the default), or to automatically turn on when running on DC. Notice that in DC mode, any direction- or speed-dependent behaviors will continue to operate as normal.
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

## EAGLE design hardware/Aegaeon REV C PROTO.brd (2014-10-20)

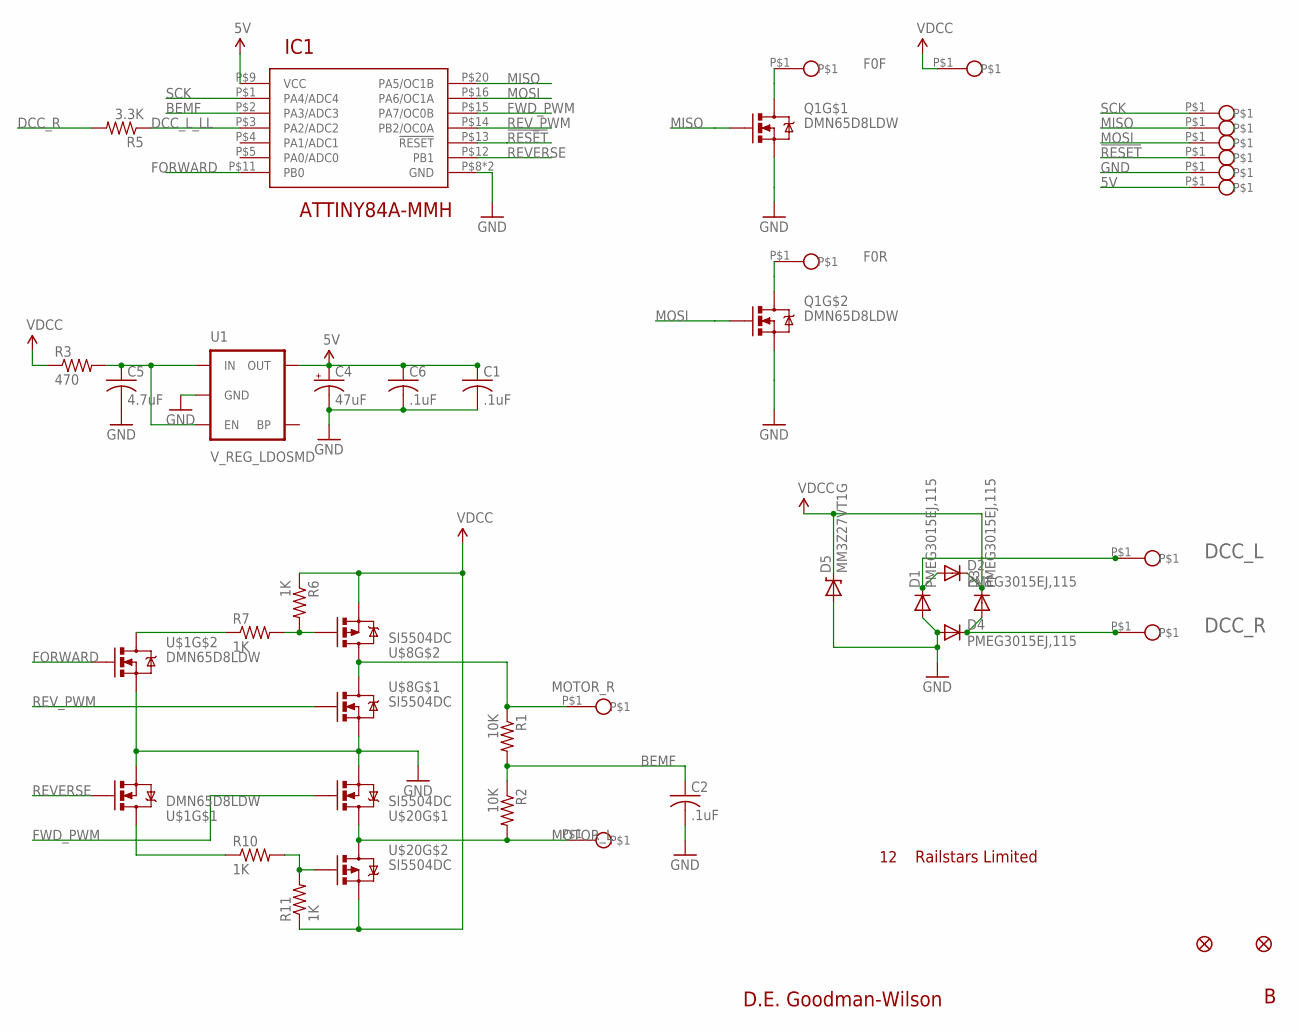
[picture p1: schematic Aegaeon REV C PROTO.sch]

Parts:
C1: .1uF; C0201
C2, C6: .1uF; C0402
C4: 47uF; CPOL0603
C5: 4.7uF; C0603
D1, D2, D3, D4: PMEG3015EJ,115; SOD-323
D5: MM3Z27VT1G; SOD-323
DCC_L: PAD1MM; LED_SOLDER_PAD
DCC_R: PAD1MM; LED_SOLDER_PAD
IC1: ATTINY84A-MMH; VQFN-20
JP2, JP4: FIDUCIALUFIDUCIAL; MICRO-FIDUCIAL
Q1: DMN65D8LDW; SOT363
R1, R2: 10K; R0201
R3: 470; R0201
R5: 3.3K; R0201
R6, R7, R10, R11: 1K; R0201
U1: V_REG_LDOSMD; SOT23-5
U$1: DMN65D8LDW; SOT363
U$2, U$3, U$5, U$10, U$11: PAD1MM; LED_SOLDER_PAD
U$8, U$20: SI5504DC; 1206-8
U$14, U$15, U$16, U$17, U$18, U$19: PAD.75MM; POGO_PAD

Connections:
5V: C1.1, C4.1 (+), C6.1, IC1.P$9 (VCC), U1.5 (OUT), U$19.P$1
!RESET: IC1.P$13 (!RESET), U$17.P$1
BEMF: C2.1, IC1.P$2 (PA3/ADC3), R1.2, R2.1
DCC_L: D1.1 (C), D2.2 (A), DCC_L.P$1
DCC_L_LL: IC1.P$3 (PA2/ADC2), R5.1
DCC_R: D3.2 (A), D4.1 (C), DCC_R.P$1, R5.2
F0F: Q1.P$4 (D), U$10.P$1
F0R: Q1.P$1 (D), U$5.P$1
FORWARD: IC1.P$11 (PB0), U$1.P$5 (G)
FWD_PWM: IC1.P$15 (PA7/OC0B), U$20.P$2 (G)
GND: C1.2, C2.2, C4.2 (-), C5.2, C6.2, D1.2 (A), D4.2 (A), D5.2 (A), IC1.P$8 (GND), IC1.P$21 (GND), Q1.P$3 (S), Q1.P$6 (S), U1.2 (GND), U$1.P$3 (S), U$1.P$6 (S), U$8.P$1 (S), U$18.P$1, U$20.P$1 (S)
MISO: IC1.P$20 (PA5/OC1B), Q1.P$2 (G), U$15.P$1
MOSI: IC1.P$16 (PA6/OC1A), Q1.P$5 (G), U$16.P$1
MOTOR_L: R2.2, U$3.P$1, U$20.P$5 (D), U$20.P$6 (D), U$20.P$7 (D), U$20.P$8 (D)
MOTOR_R: R1.1, U$2.P$1, U$8.P$5 (D), U$8.P$6 (D), U$8.P$7 (D), U$8.P$8 (D)
unnamed: R6.2, R7.2, U$8.P$4 (G)
unnamed: C5.1, R3.2, U1.1 (IN), U1.3 (EN)
unnamed: R10.2, R11.2, U$20.P$4 (G)
unnamed: R10.1, U$1.P$4 (D)
unnamed: R7.1, U$1.P$1 (D)
REVERSE: IC1.P$12 (PB1), U$1.P$2 (G)
REV_PWM: IC1.P$14 (PB2/OC0A), U$8.P$2 (G)
SCK: IC1.P$1 (PA4/ADC4), U$14.P$1
VDCC: D2.1 (C), D3.1 (C), D5.1 (C), R3.1, R6.1, R11.1, U$8.P$3 (S), U$11.P$1, U$20.P$3 (S)

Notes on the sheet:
Railstars Limited
D.E. Goodman-Wilson

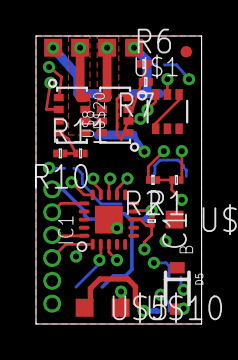
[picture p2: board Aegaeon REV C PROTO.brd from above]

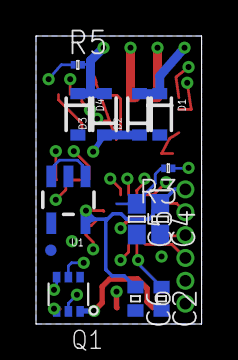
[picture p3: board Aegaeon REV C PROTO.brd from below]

Board: 4 copper layers, 9.2 x 16.0 mm, 39 parts (13 on the bottom side), 24 nets.

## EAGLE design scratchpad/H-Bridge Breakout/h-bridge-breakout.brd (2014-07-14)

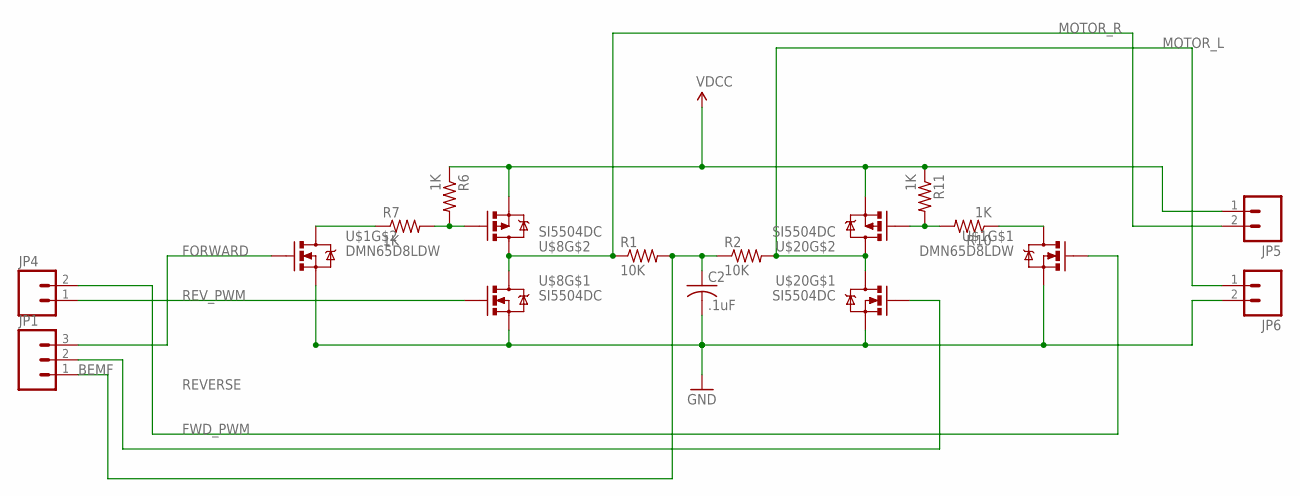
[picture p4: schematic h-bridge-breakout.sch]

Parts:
C2: .1uF; C0402
JP1: M03SCREW; SCREWTERMINAL-3.5MM-3
JP4, JP5, JP6: M023.5MM; SCREWTERMINAL-3.5MM-2
R1, R2: 10K; R0603
R6, R7, R10, R11: 1K; R0603
U$1: DMN65D8LDW; SOT363
U$8, U$20: SI5504DC; 1206-8

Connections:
BEMF: C2.1, JP1.1, R1.2, R2.1
FORWARD: JP1.3, U$1.P$5 (G)
FWD_PWM: JP1.2, U$20.P$2 (G)
GND: C2.2, JP6.2, U$1.P$3 (S), U$1.P$6 (S), U$8.P$1 (S), U$20.P$1 (S)
MOTOR_L: JP6.1, R2.2, U$20.P$5 (D), U$20.P$6 (D), U$20.P$7 (D), U$20.P$8 (D)
MOTOR_R: JP5.2, R1.1, U$8.P$5 (D), U$8.P$6 (D), U$8.P$7 (D), U$8.P$8 (D)
unnamed: R6.2, R7.2, U$8.P$4 (G)
unnamed: R10.2, R11.2, U$20.P$4 (G)
unnamed: R10.1, U$1.P$4 (D)
unnamed: R7.1, U$1.P$1 (D)
REVERSE: JP4.2, U$1.P$2 (G)
REV_PWM: JP4.1, U$8.P$2 (G)
VDCC: JP5.1, R6.1, R11.1, U$8.P$3 (S), U$20.P$3 (S)

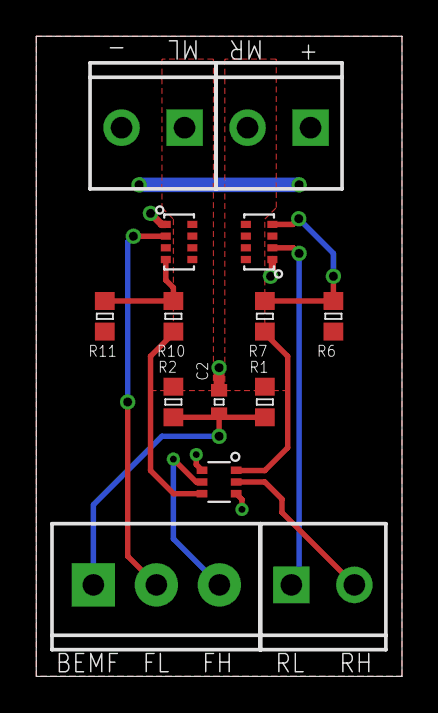
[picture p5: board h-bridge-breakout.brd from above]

Board: 2 copper layers, 20.3 x 35.6 mm, 14 parts (0 on the bottom side), 13 nets.

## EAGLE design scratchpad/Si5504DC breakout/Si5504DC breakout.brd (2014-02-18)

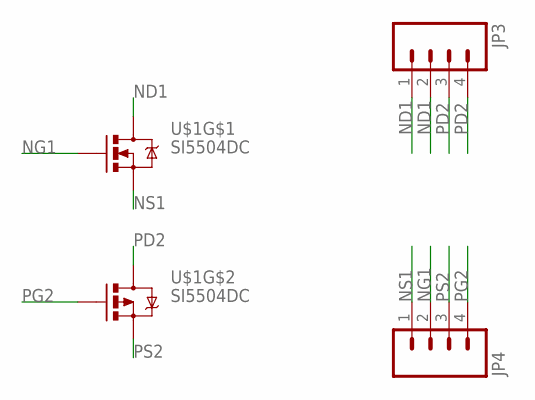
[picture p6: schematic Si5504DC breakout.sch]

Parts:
JP3, JP4: M04LOCK; 1X04_LOCK
U$1: SI5504DC; 1206-8

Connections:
ND1: JP3.1, JP3.2, U$1.P$7 (D), U$1.P$8 (D)
NG1: JP4.2, U$1.P$2 (G)
NS1: JP4.1, U$1.P$1 (S)
PD2: JP3.3, JP3.4, U$1.P$5 (D), U$1.P$6 (D)
PG2: JP4.4, U$1.P$4 (G)
PS2: JP4.3, U$1.P$3 (S)

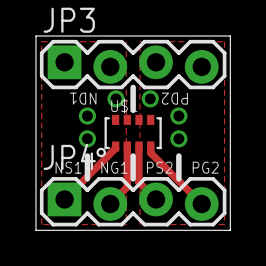
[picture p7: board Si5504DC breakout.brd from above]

Board: 2 copper layers, 10.8 x 10.8 mm, 3 parts (0 on the bottom side), 6 nets.

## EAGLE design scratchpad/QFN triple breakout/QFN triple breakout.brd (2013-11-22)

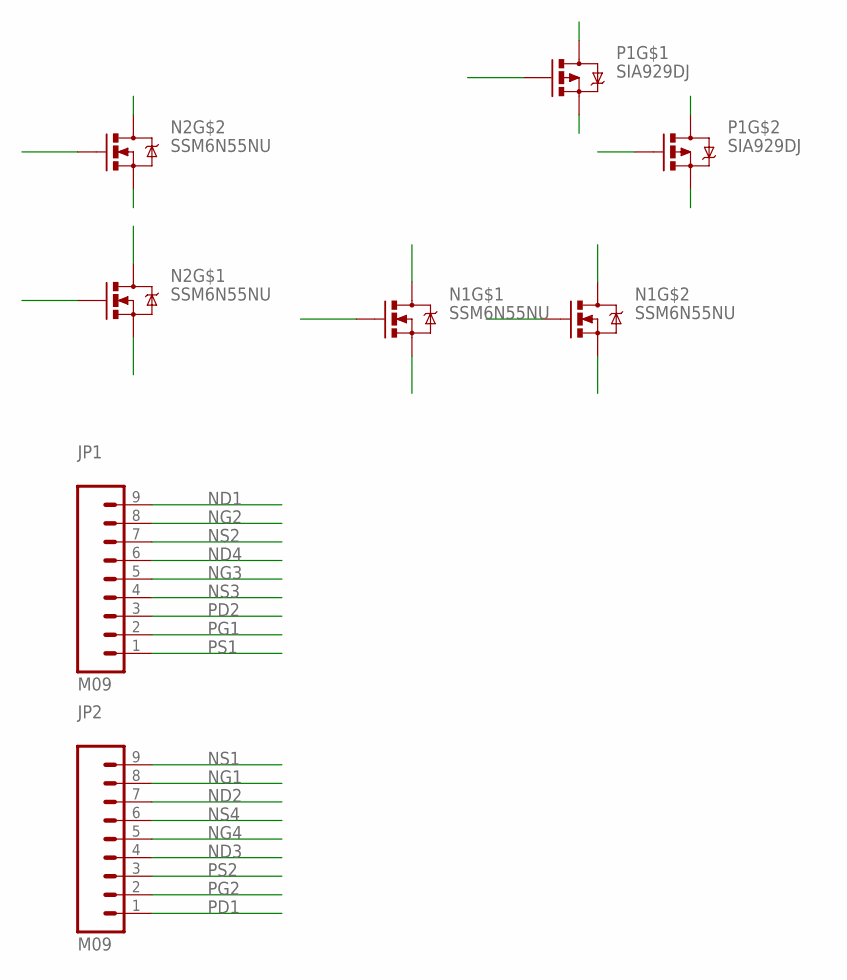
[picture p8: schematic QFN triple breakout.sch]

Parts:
JP1, JP2: M09; 1X09
N1, N2: SSM6N55NU; UDFN6
P1: SIA929DJ; SC70-6L

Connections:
ND1: JP1.9, N2.D2 (D), N2.D2$2 (D)
ND2: JP2.7, N2.D1 (D), N2.D1$1 (D)
ND3: JP2.4, N1.D1 (D), N1.D1$1 (D)
ND4: JP1.6, N1.D2 (D), N1.D2$2 (D)
NG1: JP2.8, N2.G2 (G)
NG2: JP1.8, N2.G1 (G)
NG3: JP1.5, N1.G1 (G)
NG4: JP2.5, N1.G2 (G)
NS1: JP2.9, N2.S2 (S)
NS2: JP1.7, N2.S1 (S)
NS3: JP1.4, N1.S1 (S)
NS4: JP2.6, N1.S2 (S)
PD1: JP2.1, P1.D1 (D), P1.D1$2 (D)
PD2: JP1.3, P1.D2 (D), P1.D2$2 (D)
PG1: JP1.2, P1.G1 (G)
PG2: JP2.2, P1.G2 (G)
PS1: JP1.1, P1.S1 (S)
PS2: JP2.3, P1.S2 (S)

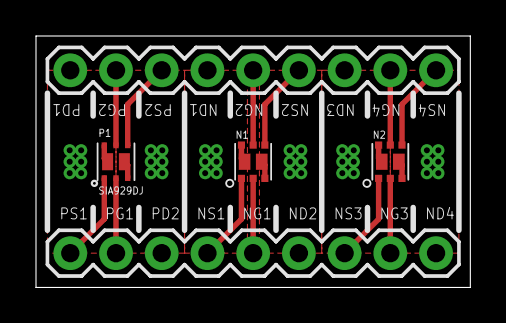
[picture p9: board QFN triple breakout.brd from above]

Board: 2 copper layers, 24.1 x 14.0 mm, 5 parts (0 on the bottom side), 18 nets.

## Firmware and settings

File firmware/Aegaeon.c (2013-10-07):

#include <avr/io.h>
#include <avr/interrupt.h>
#include <avr/eeprom.h>
//#include <avr/wdt.h>

#include <stdint.h>
#include "DCC_Hardware.h"
#include "DCC_Decoder.h"
#include "DCC_Config.h"
#include "DCC_Packet.h"
#include "Motor.h"
#include "FX.h"
#include "reset.h"

//~80microseconds to process a packet (so far; only handling motor control)
//30microseconds to process non-intersting packets --- this includes time taken out for interrupts!
//10-40 microseconds to process a bit.
//3-4 ms to load RAM cache. We could optimize this.

//GLOBALS!
int8_t _goal_speed,  _current_speed;
//int8_t _max_speed;
uint8_t DCC_CV29;
uint8_t DCC_consist_address;
uint8_t DCC_address_kind;
uint8_t BEMF_cutoff, BEMF_period;
uint8_t FX_Active;
uint8_t FX[2];
uint8_t FX_Brightness[2];
uint8_t FX_Dim_Brightness[2];
uint8_t FX_Animation[2];
uint8_t FX_Animation_Frame[2];
uint8_t FX_Period[2];


int16_t BEMF_Kp, BEMF_Ki;
uint16_t BEMF_Kf, BEMF_Kf_consist;
uint16_t DCC_address;
uint32_t FX_Prev_Time[2];
uint32_t _prev_time;
uint32_t _jog_time;
uint32_t _kick_start_time;
uint32_t DCC_accel_rate;
uint32_t DCC_decel_rate;
uint32_t accum;
uint32_t DCC_forward_trim;
uint32_t DCC_reverse_trim;

volatile int8_t _bemf_speed;
volatile uint8_t buf_sel, ready_buf, softcount, DCC_flags, Output_Match[2], Output_Match_Buf[2];
volatile uint16_t _micros_rollover;
volatile uint32_t _millis_counter, _micros_counter, _prev_bemf_time;
uint8_t DCC_speed_table[127];
volatile DCC_Packet_t DCC_rx_buffer[2];

//uint16_t free;

///////

#ifndef TESTING
int main(void)
{
#ifndef __DEBUG
    OSCCAL = eeprom_read_byte((const uint8_t*)0x1FF);   //<-- THE PROBLEM IS HERE!?
#endif
    
    //wdt_enable(WDTO_2S); //set a very long timeout.
    
    cli();
    
    //TODO uncertain about the necessity of the following
    //set all unused pins to inputs, enable pullups.
    //at boot time, all pins are set to inputs
    //the pins not used are: PA0, PA1, PA4, PA5 (:M and :C only), PA6 (:M and :C only), PB0, and PB3 (reset)
    PORTA |= ( (1 << PA0) | (1 << PA1) | (1 << PA4) );
    PORTB |= ( (1 << PB0) | (1 << PB3) );
    
    //MCUSR = 0;
    
    
    
    //first thing first, call the setup functions
    DCC_Config_Initialize();
    //wdt_reset();
    DCC_Hardware_Initialize();
    //wdt_reset();
    //DCC_Decoder_Initialize(); //nothing gets done here, everything is already initialized to 0!
    Motor_Initialize();
    //wdt_reset();
#ifdef USE_FX
    FX_Initialize();
#endif
    //wdt_reset();
    //now set up watchdog timer
    //wdt_enable(WDTO_15MS);
    
    sei();
    //wdt_enable(WDTO_15MS);
    
    while(1)
    {
        DCC_Decoder_Update();
        //wdt_reset(); //feed the watchdog
        Motor_Update();
        //wdt_reset();
#ifdef USE_FX
        FX_Update();
#endif
        //wdt_reset(); //feed the watchdog
    }
}
#endif

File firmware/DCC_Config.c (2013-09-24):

#include <avr/io.h>
#include <avr/eeprom.h>
#include <avr/pgmspace.h>
#include <stdint.h>
#include "DCC_Config.h"
#include "DCC_Decoder.h"
#include "Motor.h"
#include "FX.h"
#include "globals.h"

uint8_t const PROGMEM _defaults[] = {
    0x00, // internal flag byte, allows CV1 to be at address 01
    0x03, // PRIMARY_ADDRESS			1	//mandatory,	3,	RW,	Uniform
    0x01, // V_START					2	//recommended,	x,	RW
    0x00, // ACCELERATION_RATE		3	//recommended,	x,	RW
    0x00, // DECELERATION_RATE		4	//recommended,	x,	RW
    0x00, // V_HIGH					5	//optional,		x,	RW
    0x00, // V_MID					6	//optional,		x,	RW
    DECODER_VERSION, // MANUFACTURER_VERSION	7	//mandatory,	x,	RO
    MANUFACTURER_ID, // MANUFACTURER_ID			8	//mandatory,	x,	RO, Uniform
    0x00, // TOTAL_PWM_PERIOD		9	//optional,		x,	RW
    0x00, // EMF_FEEDBACK_CUTOUT		10	//required,		x,	RW
    
    0x00, // PACKET_TIME_OUT_VALUE	11	//optional,		x,	RW
    0x02, // POWER_SOURCE_CONVERSION	12	//optional,		x,	RW, Uniform
    0x00, // ALTERNATE_MODE_FUNCTION_STATUS_F1_F8		13	//optional,		x,	RW, Uniform
    0x03, // ALTERNATE_MODE_FUNCTION_STATUS_FL_F9_F12		14	//optional,		x,	RW, Uniform
    0x00, // DECODER_LOCK_1			15	//optional,		x,	RW, Uniform
    0x00, // DECODER_LOCK_2			16	//optional,		x,	RW, Uniform
    0x00, // EXTENDED_ADDRESS_MSB		17	//optional,		x,	RW, Uniform
    0x00, // EXTENDED_ADDRESS_LSB		18	//optional,		x,	RW, Uniform
    0x00, // CONSIST_ADDRESS			19	//optional,		x,	RW, Uniform
    0x00, // RESERVED				20	//RESERVED
    
    0x00, // CONSIST_ADDRESS_ACTIVE_FOR_F1_F8		21	//optional,		x,	RW, Uniform
    0x00, // CONSIST_ADDRESS_ACTIVE_FOR_FL_F9_F12		22	//optional,		x,	RW, Uniform
    0x00, // ACCELERATION_ADJUSTMENT	23	//optional,		x,	RW, Uniform
    0x00, // DECELERATION_ADJUSTMENT	24	//optional,		x,	RW, Uniform
    0x00, // SPEED_TABLE/MIDRANGE_SPEED_STEP				25	//optional,		x,	RW, Uniform
    0x00, // RESERVED				26	//RESERVED
    0x00, // DECODER_AUTOMATIC_STOPPING_CONFIG		27	//optional,		x,	RW, Uniform
    0x00, // BI_DIRECTIONAL_COMMUNICIMATION_CONFIG		28	//optional,		x,	RW, Uniform
    0x06, // CONFIGURATION_DATA		29	//mandatory*,	x,	RW, Uniform
    0x00, // ERROR_INFORMATION		30	//optional,		x,	RW, Uniform
    
    0x00, // INDEX_HIGH_BYTE			31	//optional,		x,	RW, Uniform
    0x00, // INDEX_LOW_BYTE			32	//optional,		x,	RW, Uniform
    0x00, // OUTPUT_LOCATION_FLF		33	//optional,		x,	RW, Uniform
    0x03, // OUTPUT_LOCATION_FLR		34	//optional,		x,	RW, Uniform
    0x04, // OUTPUT_LOCATION_FL1		35	//optional,		x,	RW, Uniform
    0x08, // OUTPUT_LOCATION_FL2		36	//optional,		x,	RW, Uniform
    0x10, // OUTPUT_LOCATION_FL3		37	//optional,		x,	RW, Uniform
    0x04, // OUTPUT_LOCATION_FL4		38	//optional,		x,	RW, Uniform
    0x08, // OUTPUT_LOCATION_FL5		39	//optional,		x,	RW, Uniform
    0x10, // OUTPUT_LOCATION_FL6		40	//optional,		x,	RW, Uniform
    
    0x20, // OUTPUT_LOCATION_FL7		41	//optional,		x,	RW, Uniform
    0x40, // OUTPUT_LOCATION_FL8		42	//optional,		x,	RW, Uniform
    0x00, // OUTPUT_LOCATION_FL9		43	//optional,		x,	RW, Uniform
    0x00, // OUTPUT_LOCATION_FL10	44	//optional,		x,	RW, Uniform
    0x00, // OUTPUT_LOCATION_FL11	45	//optional,		x,	RW, Uniform
    0x00, // OUTPUT_LOCATION_FL12	46	//optional,		x,	RW, Uniform
    
    0x01, // CV_OPS_MODE_BASIC_ACK	47	//optional,		x,	RW
    
    0x01, // CV_OUTPUT_1_DIRECTION_RULE17                48
    0xFF, // CV_OUTPUT_1_BRIGHTNESS         49	//optional,		x,	RW
    0xFF, // CV_OUTPUT_1_RULE_17_BRIGHTNESS	50	//optional,		x,	RW
    0x00, // CV_OUTPUT_1_FX             	51	//optional,		x,	RW
    0x3E, // CV_OUTPUT_1_PERIOD 			52, default 2 seconds
    
    0x02, // CV_OUTPUT_2_DIRECTION_RULE17   53
    0xFF, // CV_OUTPUT_2_BRIGHTNESS     	54	//optional,		x,	RW
    0xFF, // CV_OUTPUT_2_RULE_17_BRIGHTNESS	default 0.2     55	//optional,		x,	RW
    0x00, // CV_OUTPUT_2_FX  				56	//optional,		x,	RW
    0x3E, // CV_OUTPUT_1_PERIOD				57, default 2 seconds (62ms)
    
    FIRMWARE_REVISION, // CV_FIRMWARE_REVISION			58
    0x01, // CV_MOTOR_FREQUENCY			59
    
    0x64, // CV_BEMF_PERIOD, default 100ms	60	//optional,		x,	RW
    0x32, // CV_BEMF_PGAIN, default 40%	61	//optional,		x,	RW
    0x18, // CV_BEMF_IGAIN, default 10%  62	//optional,		x,	RW
    0xFF, // CV_BEMF_FGAIN, default 100%	63	//optional,		x,	RW
    0x98, // CV_BEMF_FGAIN_CONSIST, default 60% 64	//optional,		x,	RW
    0x00, // KICK_START				65	//optional,		x,	RW
    0x00, // FORWARD_TRIM			66	//optional,		x,	RW
    0x01, // SPEED_TABLE_1			67	//optional,		x,	RW
    0x0A, // SPEED_TABLE_2			68	//optional,		x,	RW
    0x13, // SPEED_TABLE_3			69	//optional,		x,	RW
    0x1D, // SPEED_TABLE_4			70	//optional,		x,	RW
    
    0x26, // SPEED_TABLE_5			71	//optional,		x,	RW
    0x30, // SPEED_TABLE_6			72	//optional,		x,	RW
    0x39, // SPEED_TABLE_7			73	//optional,		x,	RW
    0x42, // SPEED_TABLE_8			74	//optional,		x,	RW
    0x4C, // SPEED_TABLE_9			75	//optional,		x,	RW
    0x55, // SPEED_TABLE_10			76	//optional,		x,	RW
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

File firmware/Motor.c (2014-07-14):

#include <avr/io.h>
#include <avr/interrupt.h>
#include <avr/eeprom.h>
#include <util/atomic.h>
#define F_CPU 8000000UL  // 8 MHz
#include <util/delay.h>

#include <stdint.h>
#include "DCC_Config.h"
#include "DCC_Decoder.h"
#include "Motor.h"
#include "globals.h"

#define ENABLE (1<<PB1)
#define FX_SHUNTING (1<<6)

volatile uint8_t sample, sample_ready, min_ADC;
int16_t sum_err;

uint8_t _eStop;

//consider the algorithm at http://www.advice1.com/reference/pidalgorithmref.html

uint8_t PDFF(int16_t set, int16_t measured)
{
    //    int16_t i_set = set;
    //    int16_t i_measured = measured;
    if (0 == set) //setting a 0 voltage, don't bother.
    {
        //but do measure and set the minimum measured voltage!
        //min_ADC = measured;
        return 0;
    }
    
    //check to see if BEMF is enabled
    
    //check to see if we are above the cutoff speed
    
    int16_t err = set - measured;
    sum_err += err;
    //prevent windup
    if (sum_err > 1024) sum_err = 1024;
    else if (sum_err < -1024) sum_err = 1024;
    
    int16_t iterm;
    if(sum_err < 0)
    {
        iterm = -1 * (BEMF_Ki * sum_err) / 256;
        iterm *= -1;  //TODO WTF is this?
    }
    else
    {
        iterm = (BEMF_Ki * sum_err) / 256;
    }
    
    int16_t fterm;
    if(DCC_consist_address) //if in a consist
    {
        fterm = ((BEMF_Kf_consist * (uint16_t)set) / 256) - measured;
    }
    else
    {
        fterm = ((BEMF_Kf * (uint16_t)set) / 256) - measured;
        
    }
    
    int16_t pterm = (BEMF_Kp * fterm) / 256;
    
    int16_t retval = iterm + pterm + set;
    if(retval < 0) return 0;
    else if(retval > 255) return 255;
    else return retval;
}

//                  PB0 (fwd)   PB1 (rev)   PA7 (fpwm)  PB2 (rpwm)
//FORWARD =         HIGH        LOW         HIGH        LOW
//REVERSE =         LOW         HIGH        LOW         HIGH
//BRAKE   =         HIGH        HIGH        LOW         LOW
//  or              LOW         LOW         HIGH        HIGH
//COAST   =         LOW         LOW         LOW         LOW
//I think.

void Motor_Initialize(void)
{
    //pre-condition: DCC_Config_Initialize has been called first. Interrupts have been disabled
    
    //first, compute the accel and decel factors.
    //TODO THIS MAY HAVE TO BE CALLED BY DCC_Config if these CV values change!!
    // (the contents of CV#3*.896)/(number of speed steps in use) = accel factor in seconds/speed_step, a weird unit of measure.
    
    //do other things to set up the hardware.
    //on ATtiny84A, setup TIMER0 for both motor control PWM on output compare B and a millis timer on compare match overflow
    
    //set PB0, PB1, PA7, and PB2 to output, and bring all low
    DDRB |= (1 << DDB0) | (1 << DDB1) | (1 << DDB2);
    DDRA |= (1 << DDA7);
    PORTB &= ~(1 << PB0) & ~(1 << PB1) & ~(1 << PB2); //set all these LOW
    PORTA &= ~(1 << PA7);
    
    
    TCCR0A = (1 << WGM00); // phase correct PWM
    if(eeprom_read_byte((const uint8_t*)CV_MOTOR_FREQUENCY)) // positive value = high frequency, use fast PWM
        TCCR0A |= (1 << WGM01);
    TCCR0B = (1 << CS00); //use /1 prescaler
    
    TCNT0 = 0;
    OCR0A = 0x00; //turn right low-side switch off.
    OCR0B = 0x00; //turn left low-side switch off
    
    TIMSK0 |= (1 << TOIE0); //enable overflow interrupt so we can count micros
    
#ifdef USE_BEMF
    //enable the ADC for BEMF measurement
    DIDR0 |= (1 << ADC3D);
    ADCSRA |= (1 << ADEN) | (1 << ADIE) | (1 << ADPS2) | (1 << ADPS0); //enable ADC, enable interrupt, set prescalar to 32 to get a clock of 250KHz. See pg 135 of ATtiny84a manual
    ADCSRB |= (1 <<  ADLAR); //left justified ADC output for 8-bit reads
    ADMUX = 0x03; //enable ADC3 for analog conversion, use VCC as reference.
#endif //USE_BEMF
    
    _eStop = 0;
    _current_speed = _goal_speed = 1; //forward stop
    min_ADC = 0x93;
}

#ifdef USE_BEMF
ISR(ADC_vect) //ISR for ADC conversion complete
{
    sample = (uint8_t)((1036*(ADCH - min_ADC))>>8);
    _prev_bemf_time = millis(); //set the time of last measurement
    sample_ready = 1;
}
#endif //USE_BEMF

ISR(TIM0_OVF_vect)
{
    _micros_rollover += 32; //at 8MHz, /1 prescaler, it takes 32 microseconds to cycle through
    _micros_counter += 32;
    if (_micros_rollover >= 1000) //update millis
    {
        ++_millis_counter;
        _micros_rollover -= 1000;
    }
    
#ifdef USE_FX
    //also handle FX
    if (softcount++ == 0)
    {
        Output_Match[0] = Output_Match_Buf[0];
        Output_Match[1] = Output_Match_Buf[1];
        if (Output_Match[0])
            PORTA |= (1 << PA5); //only turn on if match is non-zero! Prevents flicker when should be off.
        if (Output_Match[1])
            PORTA |= (1 << PA6);
    }
    
    if (Output_Match[0] == softcount) //just rolled over, turn output off
    {
        PORTA &= ~(1 << PA5);
    }
    if (Output_Match[1] == softcount) //just rolled over, turn output off
    {
        PORTA &= ~(1 << PA6);
    }
#endif //USE_FX
    
}

uint32_t millis(void)
{
    uint32_t m;
    
    ATOMIC_BLOCK(ATOMIC_FORCEON)
    {
        m = _millis_counter;
    }
    return m;
}

uint32_t micros(void)
{
    uint32_t m;
    
    ATOMIC_BLOCK(ATOMIC_RESTORESTATE)
    {
        m = _micros_counter;
    }
    return m;
}


void Motor_EStop(int8_t dir)
{
#ifdef USE_MOTOR
    //NMRA requires that we remove power from motor. We do this by setting out motor lines LOW.
    TCCR0A &= ~(1 << COM0A0) & ~(1 << COM0A1) & ~(COM0B0) & ~(COM0B1); //disconnect PWM from timer
    PORTB &= ~(1 << PB0) & ~(1 << PB1) & ~(1 << PB2); //force all four motor control lines LOW, turns off motor.
    PORTA &= ~(1 << PA7); //these two lines may not be necessary. Possibly even dangerous.

#endif //USE_MOTOR
    
    _eStop = 1;
    if (dir >= 0)
        _current_speed = _goal_speed = 1; //immediate forward stop
    else
        _current_speed = _goal_speed = -1; //immediate reverse stop
    //_voltage_level = _voltage_adjust = 0; //make sure we don't re-energize!
}

//in all of the following, 0 = stop; 1 is first movement step.

//void Motor_Set_Speed_By_DCC_Speed_Step_14(int8_t notch)
//{
//	Motor_Set_Speed_By_DCC_Speed_Step_128( (notch*18) >> 1);
//}

//wants a value in the range 0..27

void Motor_Set_Speed_By_DCC_Speed_Step_28(int8_t notch)
{
    //valid range is 1..29, -1..-29
    uint8_t new_notch = notch;
    if (notch < 0)
        new_notch = -notch;
    else
        new_notch = notch;
    
    if (new_notch > 1) //don't mess with notches 0 or 1, leave those be.
    {
        if (new_notch >= 29) //our rounding algorithm messes up on this case: it sets 29 to 126, which is wrong. This is the expedient fix.
            new_notch = 127;
        else
            new_notch = ((new_notch - 1) *9) >> 1; //notch-1 * 4.5
    }
    
    if (notch < 0) //reverse it again
        new_notch = -new_notch;
    Motor_Set_Speed_By_DCC_Speed_Step_128(new_notch);
}
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

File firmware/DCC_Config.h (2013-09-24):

#include <stdint.h>

#ifndef __DCC_CONFIG_H__
#define __DCC_CONDIG_H__

//set up decoder options for conditional compilation

//BEMF is only availabnle on decoders with motor outputs, at this time
// the 'M and 'L2
#if defined(__AEGAEON_M) || defined(__AEGAEON_L2)
#define USE_BEMF
#define USE_MOTOR
#endif

//FX are only available on decoders with function outputs, at this time,
// The 'L2 and the 'C
#if defined(__AEGAEON_M) || defined(__AEGAEON_L2)
#define USE_FX
#endif

//Some decoders use H-Bridge to drivwe functions, currently only the C
#if defined(__AEGAEON_C)
#define USE_MOTOR_FOR_FX
#endif



#ifdef __AEGAEON_L2
#define DECODER_VERSION	0x05 //Aegaeon:L2
#else
#ifdef __AEGAEON_M
#define DECODER_VERSION 0x01 //Aegaeon:M
#else
#ifdef __AEGAEON_C
#define DECODER_VERSION 0x04 //Aegaeon:C
#else
#error No decoder defined!
#endif
#endif
#endif

#define MANUFACTURER_ID	0x5B //Railstars Limited
#define FIRMWARE_REVISION 0x01


//CV 29 helpers
#define CV29_REVERSE			(DCC_CV29 & 0x01)
#define CV29_28_SPEEDSTEPS		(DCC_CV29 & 0x02)
#define CV29_POWER_CONVERSION   (DCC_CV29 & 0x04)
#define CV29_RAILCOM			(DCC_CV29 & 0x08)
#define CV29_FANCY_SPEED_CURVE  (DCC_CV29 & 0x10)
#define CV29_LONG_ADDRESSING    (DCC_CV29 & 0x20)
#define CV29_RESERVED1			(DCC_CV29 & 0x40)
#define CV29_RESERVED2			(DCC_CV29 & 0x80)

#ifdef RAILCOM
#define CV29_MASK               (CV29_REVERSE | CV29_POWER_CONVERSION | CV29_FANCY_SPEED_CURVE | CV29_LONG_ADDRESSING)
#else
#define CV29_MASK               0x35
#endif

//CV definitions
#define CV_PRIMARY_ADDRESS		1	//mandatory,	3,	RW,	Uniform
#define CV_V_START			2	//recommended,	x,	RW
#define CV_ACCELERATION_RATE		3	//recommended,	x,	RW
#define CV_DECELERATION_RATE		4	//recommended,	x,	RW
#define CV_V_HIGH			5	//optional,		x,	RW
#define CV_V_MID			6	//optional,		x,	RW
#define CV_MANUFACTURER_VERSION         7	//mandatory,	x,	RO
#define CV_MANUFACTURER_ID		8	//mandatory,	x,	RO, Uniform
//#define CV_TOTAL_PWM_PERIOD		9	//optional,		x,	RW
#define CV_EMF_FEEDBACK_CUTOUT		10	//required,		x,	RW

#define CV_PACKET_TIME_OUT_VALUE	11	//optional,		x,	RW
//#define CV_POWER_SOURCE_CONVERSION	12	//optional,		x,	RW, Uniform
#define CV_ALTERNATE_MODE_FUNCTION_STATUS_F1_F8		13	//optional,		x,	RW, Uniform
#define CV_ALTERNATE_MODE_FUNCTION_STATUS_FL_F9_F12	14	//optional,		x,	RW, Uniform
#define CV_DECODER_LOCK_KEY		15	//optional,		x,	RW, Uniform
#define CV_DECODER_LOCK_LOCK		16	//optional,		x,	RW, Uniform
#define CV_EXTENDED_ADDRESS_MSB		17	//optional,		x,	RW, Uniform
#define CV_EXTENDED_ADDRESS_LSB		18	//optional,		x,	RW, Uniform
#define CV_CONSIST_ADDRESS			19	//optional,		x,	RW, Uniform
#define CV_RESERVED_20				20	//RESERVED

#define CV_CONSIST_ADDRESS_ACTIVE_FOR_F1_F8     21	//optional,		x,	RW, Uniform
#define CV_CONSIST_ADDRESS_ACTIVE_FOR_FL_F9_F12	22	//optional,		x,	RW, Uniform
//#define CV_ACCELERATION_ADJUSTMENT	23	//optional,		x,	RW, Uniform
//#define CV_DECELERATION_ADJUSTMENT	24	//optional,		x,	RW, Uniform
//#define CV_SPEED_TABLE				25	//optional,		x,	RW, Uniform
//#define CV_MID_RANGE_SPEED_STEP		25	//optional,		x,	RW, Uniform //same as the one above, but has two purposes
#define CV_RESERVED_26				26	//RESERVED
//#define CV_DECODER_AUTOMATIC_STOPPING_CONFIG		27	//optional,		x,	RW, Uniform
//#define CV_BI_DIRECTIONAL_COMMUNICIMATION_CONFIG		28	//optional,		x,	RW, Uniform
#define CV_CONFIGURATION_DATA		29	//mandatory*,	x,	RW, Uniform
//#define CV_ERROR_INFORMATION		30	//optional,		x,	RW, Uniform

//#define CV_INDEX_HIGH_BYTE			31	//optional,		x,	RW, Uniform
//#define CV_INDEX_LOW_BYTE			32	//optional,		x,	RW, Uniform
#define CV_OUTPUT_LOCATION_FLF		33	//optional,		x,	RW, Uniform
#define CV_OUTPUT_LOCATION_FLR		34	//optional,		x,	RW, Uniform
#define CV_OUTPUT_LOCATION_FL1		35	//optional,		x,	RW, Uniform
#define CV_OUTPUT_LOCATION_FL2		36	//optional,		x,	RW, Uniform
#define CV_OUTPUT_LOCATION_FL3		37	//optional,		x,	RW, Uniform
#define CV_OUTPUT_LOCATION_FL4		38	//optional,		x,	RW, Uniform
#define CV_OUTPUT_LOCATION_FL5		39	//optional,		x,	RW, Uniform
#define CV_OUTPUT_LOCATION_FL6		40	//optional,		x,	RW, Uniform

#define CV_OUTPUT_LOCATION_FL7		41	//optional,		x,	RW, Uniform
#define CV_OUTPUT_LOCATION_FL8		42	//optional,		x,	RW, Uniform
#define CV_OUTPUT_LOCATION_FL9		43	//optional,		x,	RW, Uniform
#define CV_OUTPUT_LOCATION_FL10		44	//optional,		x,	RW, Uniform
#define CV_OUTPUT_LOCATION_FL11		45	//optional,		x,	RW, Uniform
#define CV_OUTPUT_LOCATION_FL12		46	//optional,		x,	RW, Uniform

#define CV_OPS_MODE_BASIC_ACK           47

#define CV_OUTPUT_1_DIRECTION_RULE17    48
#define CV_OUTPUT_1_BRIGHTNESS  	    49	//optional,		x,	RW
#define CV_OUTPUT_1_RULE_17_BRIGHTNESS  50	//optional,		x,	RW
#define CV_OUTPUT_1_FX                  51	//optional,		x,	RW
#define CV_OUTPUT_1_PERIOD              52
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

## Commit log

2013-07-14 Improved the debug build by automatically cutting off features that interfere with debugging.
    [DCC_Hardware.c, Motor.c]
2013-07-14 Adding files for automating clock calibration and firmware installation. This all needs to be organized pretty badly
    [TcfTransactionLog.csv, rc_calib.obj]
2013-07-14 Added schematics and PCB layouts for latest version of prototypes and production types.
    [Aegaeon REV B 20130130 PROTO.brd, Aegaeon REV B 20130130 PROTO.sch, Aegaeon REV B 20130222.brd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]
2013-07-14 Clock calibration and install script working!
2013-08-08 Added a breakout for the MOSFETs to the scratchpad
    [QFN triple breakout.brd, QFN triple breakout.sch]
2013-08-08 Fixed typo on silkscreen
    [QFN triple breakout.brd]
2013-08-08 Updated with OSHPark design rules
    [QFN triple breakout.brd]
2013-08-08 Added some helpful silkscreen
    [QFN triple breakout.brd]
2013-08-08 Changed a couple of part numbers to make more sense.
    [QFN triple breakout.brd, QFN triple breakout.sch]
2013-08-08 Adjusted thermal spacing
    [QFN triple breakout.brd]
2013-09-24 Fixed bug where FX outputs are never updated on 'C
    [Motor.c]
2013-10-05 Removed old decoder files, replaced with references to actual code.
    [DCC_Config.c, DCC_Config.h, DCC_Decoder.c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]
2013-10-05 Combined testing and production reset files.
    [Aegaeon.c, reset.c]
2013-10-05 Makefiles seem to be in order. Tests need to be updated to latest signatures—wow are they out of date!
2013-10-05 Unittests compile, but fail. No real surprise there as some of the interfaces have changed.
    [Aegaeon.c]
2013-10-05 Updated some of the motor output settings in tests. Moved to CLang, since GNU isn't supported on my dev platform anymore (OS X Mavericks)
2013-10-06 Cleaned up many of the motor tests, although more work to do. Refined settings for GCC to match my installs on Mavericks, which are a bit non-standard. Debugger still not quite working, although YMMV.
2013-10-07 Added Xcode project, because I was tired of banging my head against a wall getting NetBeans to work again. Left NetBeans project intact in case someone else wants to use it—it should be fine on most 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
2013-10-07 Unit tests now run, though they fail for a variety of reasons. Still lots of repair work to do to make them work with the current hardware configuration.
2013-10-07 Fixed minor logic bug in motor control.
    [Motor.c]
2013-10-07 Fixes #1 and any other tests that depend on behavior of full speed, or stopped speeds.
    [Motor.c]
2013-10-07 Added hardware defs and test for motor deenergized at start.
2013-10-07 Added hardware defs to testing motor direction, and have begun updating motor tests to proeprly test for this now. Previously, direction was tied up with the PWM output. New method of testing is indp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
2013-10-09 Fixed a problem with (MotorTests, TestAccelDecel_v1)
2013-10-09 Added better comments to estop(). Fixed estop test to reflect actual conditions during an estop.
    [Motor.c]
2013-10-09 Fixed the motor initialization test to reflect that initial conditions should be braked, not deenergized
2013-10-09 Fixed a typo in (MotorTests, Initialization)
2013-10-10 Whitespaces changes to motor.c only.
2013-10-11 Made (NMRAMotorDecoderTests, PagedModeArbitraryCVWrite) more sophisticated—can be changed for any CV easily.
2013-10-11 Closes #14. The problem, in fact, was a combination of bad code and bad tests. Basically, the direction flag in CV19 was being set wrong and tested wrong! But the reinforcing tests did eventually cat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
    [DCC_Decoder.c]
2013-10-12 Adding circuit.jar simulation of H-Bridge pursuant to solving #17.
2013-10-24 Added intrinsic diodes to MOSFETs in simulation.
2013-10-25 Added dead time delay to motor outputs when switching direction.
2013-11-22 Fixed error on QFN triple breakout silk.
    [QFN triple breakout.brd]
2013-11-25 Added a breakout board for the SI5504DC MOSFET half-bridge.
    [Si5504DC breakout.brd, Si5504DC breakout.sch]
2013-11-25 Initial commit for H-Bridge designed with SI5504DC parts.
    [Aegaeon REV B 20130130 PROTO.brd, Aegaeon REV B 20130130 PROTO.sch]
2014-02-18 Moved vias, and added solder resist to tent vias.
    [Si5504DC breakout.brd]
2014-03-02 Working on the layout a bit? Lost track of where I was.
    [Aegaeon REV B 20130130 PROTO.brd]
2014-03-04 Redesigning the H-Bridge. This one seems to work under test.
    [Aegaeon REV B 20130130 PROTO.brd, Aegaeon REV B 20130130 PROTO.sch]
2014-03-04 Set up new defines for desired motor output states.
2014-03-04 Improved motor initialization test—begins coasting, not braked
2014-03-04 Motor initialization passes
2014-03-04 Added motor shootthru tests
2014-03-04 Timers should be hooked up correctly now. Timer outputs need to be wired.
    [Motor.c]
2014-03-05 Lots of logic fixes to motor control code. Not entirely confident that they are right. At all.
    [Motor.c]
2014-03-05 Fixed some motor checking constants
2014-03-05 More motor constant fixes
2014-03-05 Improved motor tests. All logic tests pass. Crazy. This can't be right.
2014-04-14 Added a h-bridge breakout board to the scratchpad.
    Just built one of these, and the darned thing doesn't seem to work. A bit mystified as to why that might be.
    [h-bridge-breakout.brd, h-bridge-breakout.sch]
2014-07-12 Added simulation for use with circuit.jar
2014-10-20 Unsure why this got renamed, but there it is.
    [Aegaeon REV C PROTO.brd, Aegaeon REV C PROTO.sch]
2014-10-20 Feels like we're headed down a rabbit hole.
    [Aegaeon REV C PROTO.brd]

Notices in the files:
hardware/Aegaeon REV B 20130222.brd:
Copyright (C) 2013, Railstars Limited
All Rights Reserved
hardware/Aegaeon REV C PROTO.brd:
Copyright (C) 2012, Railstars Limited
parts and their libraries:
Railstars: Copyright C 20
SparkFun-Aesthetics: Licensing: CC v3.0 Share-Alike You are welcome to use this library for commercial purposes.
